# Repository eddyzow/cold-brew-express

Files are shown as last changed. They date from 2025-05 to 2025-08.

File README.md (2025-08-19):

# Cold Brew Express

a DIY electric scooter! Features include variable speed, handlebar throttle, physical brake (not connected in the video), suspension fork for weight distribution, fast top speed, and backlit display for battery.

watch me ride it at https://youtu.be/ShZDwHqLemY?si=LHhTyD6iNOCNyVUB





For links to products in the BOM, go to this google sheet: https://docs.google.com/spreadsheets/d/1F6muKYJhtXkM0ZriuXKycPCZ0PORBCmvhVav8ENI8PE/edit?usp=sharing



## table BOM:

| Item Name | Purpose | Item Source | Quantity | Unit Cost (includes taxes) | Cost | Notes |
|:---|:---|:---|---:|:---|:---|:---|
| 36V 500W 8-Inch Brushless Scooter Hub Motor | Scooter propulsion + back wheel | Amazon | 1 | $109.76 | $109.76 | |
| Brushless Motor Controller 36V 500W 25A | Scooter motion control | Amazon | 1 | $37.18 | $37.18  | |
| 36V 10AH Battery | Scooter power | Amazon | 1 | $99.91 | $99.91  | |
| 8-Inch Pneumatic Scooter Wheel | Scooter front wheel (free-spinning) | Amazon | 1 | $27.61 | $27.61  | |
| 8mm x 150mm Steel Rod | Axle for scooter front wheel | Amazon | 1 | $6.37 | $6.37 | |
| Throttle Accessory | To control motor acceleration | Amazon | 1 | $9.45 | $9.45 | |
| 14-Inch Suspension Fork | For suspension + to connect handlebars to front wheel | Amazon | 1 | $37.50 | $37.50  | |
| 37mm Headset Bearings | To make turning handlebars smoother | Amazon | 1 | $10.63 | $10.63  | |
| 4-Line I2C LCD Display (3) | For visual feedback of speed, battery, other telemetry, etc. | Amazon | 1 | $17.87 | $17.87  | better value than a 1-pack + just in case something goes wrong |
| Flex Seal | Waterproofing housing of the scooter for rain | Home Depot | 1 | $15.92 | $15.92  | |
| Variable PVC Pipe | PVC pipe for handlebars and main steering column | Home Depot | 1 | $21.25 | $21.25  | |
| Variable Plywood | Plywood for base of the scooter + housing of battery and controller | Home Depot | 1 | $21.25 | $21.25  | |
| Wires and Connectors | For wiring electronic components to the microcontroller | Amazon | 1 | $10.63 | $10.63  | primarily JST-SM connectors, jumper wires, bullet-spade connectors. will purchase as needed |
| Screws, Nuts, Bolts | For assembling the components of the scooter together | Home Depot | 1 | $10.63 | $10.63  | |
| TOTAL | | | 14 | $435.96 | $435.96 | |

I already own some necessary parts for this project (arduino, etc) - these are not included in the BOM! I will also gladly pay any surplus costs above the grant amount!

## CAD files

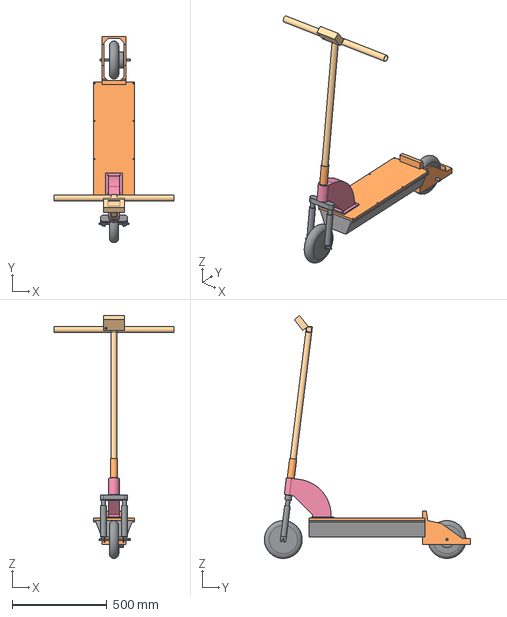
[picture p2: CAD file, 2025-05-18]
CAD Assembly Full.step
632.0 x 1088.6 x 1282.3 mm

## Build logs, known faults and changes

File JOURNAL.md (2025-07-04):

---
title: "The Cold Brew Express"
author: "Eddy Zhao (@eddyzow)"
description: "A DIY electric scooter to take me to Dunkin' Donuts."
created_at: "2025-05-14"
---

# hack club highway project 1: the cold brew express - a diy electric scooter to take me to dunkin'
_can i get a medium raspberry watermelon refresher with sparkling water instead of green tea?_

start date: 5/14/2025

total time spent so far: 43 hrs

# entry 12 (7/3/25)

and with that, the cold brew express is done! while it's not polished, i feel that i can submit becuase it is functionally "sound," i've learned all electronics and engineering that i needed for the project, and i can paint it at any time.

here's a video of me riding it: https://youtu.be/ShZDwHqLemY?si=LHhTyD6iNOCNyVUB

*time spent during session: 1 hour*

# entry 11 (7/2/25)

three home depot trips, multiple PVC pipes, duct tape, wires, and many scares later, the scooter is FUNCTIONAL!!



unfortunately the weight distribution is completely messed up and the scooter has the tendency to do wheelies before actually driving.

nonetheless i'm counting this a success! the battery and controller mounted at the bottom of the scooter. 

i'm so scared the scooter is going to break when i stand on it, so i'm probably not going to make a video of me riding it around. in hindsight I should have printed the head/neck collar with PETG or PLA-CF at the least but it seems like normal PLA is sort of holding up. i replaced multiple parts during the entire process.

the scooter's also super super super super sensitive. i think it could actually go like 20mph at max speed but i'd have to lean forward and put my weight all the way in as front as possible, but the weakest part of the scooter is just behind the front:



while the scooter's still intact, i got some pictures of the scooter.

tomorrow i'll record a demo of the scooter working, but not actualy ride it. if it breaks, then we will consider it a lesson learned. I'll fix it eventually, but undercity is in 9 days and i need to submit this before i leave since i won't be back until highway is nearly over. i'll probably wait until "eventually" to paint the scooter as well

*time spent during session: 6 hours*

# entry 10 (6/29/25)

lots has happened since the last entry... firstly the controller i bought broke (either due to it being bad or me making a mistake), so i had to buy a new one. thankfully, the new one is good, but i need to watch my wiring.

i'm rethinking adding a screen to the scooter. i think it's unnecessary because the throttle i bought has a screen by itself, but maybe just adding a screen for the cool factor could do pretty good. i might be able to use the 5v power supply from the motor controller to power the arduino.

with this sudden realization i discovered that i accidentally plugged in a red wire to the green self-learning plug a few days ago... this might have been what caused the first controller to break. upon reading the datasheet a second time, this red wire (not red in the diagram) actually is connected to the full 36V of the battery!! that means i gave a low-voltage self-learning wire 36 volts and probably fried the controller from there. 

anyways, since the motor works now, i'm going to start putting the final touches together before i flex seal and paint this baby. then, i'm going to ride it around my driveway in a video for proof before submitting it!! unfortunately my parents have forbade me from riding it on public roads (and it's illegal since my permit expired) so i can't go to dunkin with it. after i submit this and my other pull request for my pcb business card (already done) is merged, i'll have 33 highway points!! and there is one more project i wish to do before i leave for undercity -- if i can finish it on time, i'll have 40 points :)

*time spent during session: 7 hours*

# entry 9 (6/19/25)

i designed a lot of new parts! also, the chassis is officially built... just some wiring and testing left to do.



i think that getting the LCD screen incorporated may not be feasible at this moment -- my prime goal is to make sure it drives!

# entry 8 (6/15/25)

re-designed some parts today and planned out how i'm going to build the scooter! here's a picture taken by the camera onboard my bambu p1s:



... and one of the redesigned parts. this will make the weight distribution more compressive. PLA has a quite strong compression resistance, so I bet that 3d-printed parts will be able to do the trick here!



i'm going to put the scooter together in the coming days :D

time spent: about 6 hrs

# entry 7 (6/8/25)
## parts received!

parts have been received for the cold brew express! i'm printing all the 3D printed stuff as I type this -- the last thing to do is to go to home depot and get some plywood, then construct! 

there have been some errors in my planning -- the suspension fork I bought does not have any spring force and also isn't hollow at the top. it's also a little smaller than i expected. i will try to get around that. i wired up the wheel and it seems to work pretty well! the battery works great and the wheel is indeed pretty fast, with high torque. 

*time spent for this session: 2 hrs*

# hack club highway journal entry 6 (5/18/25)
## cad is done!



i believe i've cadded the entirety of the main frame of the scooter! yes, i haven't added things like the throttle but these are the parts that are added to the scooter later as accessories.
wiring will be taped down the side of the handlebar with electrical tape and routed through the hole in the neck between the head tube and the base.

here's what the internals look like:



inside are the battery and controller, which will be mounted in foam. the wires for the motor (rear) will likely be routed through a drilled hole between the rear motor fork and the base, or through the bottom of the base. i've decided that once i start putting the scooter together, i'll decide on things like that.

in the front is a suspension fork that will give the scooter a smoother ride. the display will be a standard 4 line character LCD instead of a full-fledged TFT display since i realized i will need to work with some extremely complicated electronics that i don't have the experience for at the moment. the arduino will also be mounted in the bottom of the scooter. i'm going to need some long ass jumper wires LMFAO

i still don't know how fast the scooter will get, but i'm hoping that it will do 15mph. i'm legally bound to go under 20mph anyways

i'll now be submitting this to the hack club overlords and going off to continue my neighborhood game! i should add that i'm not very experienced with cad and have only in the past imported existing gobilda files and just mated them all together with a minimally designed chassis :sob:

# hack club highway journal entry 5 (5/17/25)
## cad almost done

the CAD is almost done! i ran into a few problems that i've fixed:
- the handlebars are not sized to align with the fork (OD 30mm). i fixed this by custom-creating my own 3D printed "clamp" that will just be superglued to the fork. since i have no interest in folding up the scooter, this will work fine
- 
- i've realized that i needed to CAD the dashboard with the display.

# hack club highway journal entry 4 (5/17/25)
## it's coming together!



as you can see, i've designed many of the parts for the scooter, including the fender and neck / head tube for holding the handlebars. i will purchase a clamp separately to ensure that the handlebars can only turn left-right and cannot move up and down. the last thing i will need to CAD is the suspension fork and then i'll be all set! since i don't know how to produce these parts and i don't necessarily have access to machining tools (my robotics team has a CNC but i don't know how to fabricate the parts more complex than just sheets of metal) i'll be 3D printing them since i'm more familiar with that. 

wires will be fed from my various accessories through the crossbar in a separate tube into the deck. and i will need to secure everything using foam for the interior electronics, screws, and lots of flex seal.

from end to end the scooter is approximately 3.5 ft (1075mm) long and 3 feet (900mm) tall. i came to this value through research on what the typical scooter looks like. i think that i might be able to actually submit this for review after tonight since much of the work is done after the design has already been submitted!

# hack club highway journal entry 3 (5/17/25)
## cad updates + more!



i haven't cadded any special parts yet, like suspension, forks, etc. i think i'll forgo the suspension because apparently all the easy-to-attach suspension forks are for 10-inch wheels, and this scooter is going to have 8-inch wheels. i'll use PVC pipe instead of metal since it's easier to work with.
the part of the deck that the rider stands on is bolted to the battery and controller holder with eight 4mm gobilda screws. i hope this will be enough support.

i've learned that handlebars are angled approx. 83 degrees to the ground, so i have it turned that way.

also, i think i'll actually be 3d printing some parts, such as the fenders for the wheels. i just need to buy some flex seal to waterproof it. i might need to cad forks too, but then my concern is that the forks are not strong enough when 3D printed -- i don't have machine shop knowledge to make custom aluminum forks for my scooter.

i have a full weekend to work, so hopefully i can finish the design soon and get building!

# hack club highway journal entry 2 (5/16/25)
## APPROVED!!
the cold brew express has been approved! i just need to send in a design before i receive my parts. i will get more highway points if i make a project that actually drives!!

i've changed the BOM and feature list to better reflect my hardware knowledge + exact parts i will be getting:
- 36V 500W brushless DC hub motor with wheel and tire included: $104
- 36V 500W motor controller: $35
- 36V 10 amp-hour lithium-ion battery with 30A BMS: $94
- front free-turning wheel and tire: $30
- accessories (i.e. throttle, brake, switches, buttons): about $25
- wires and connectors: about $10
- led 2/4 line display: $10
- rgb light strip/lights: $15
- plywood base: $20
- pvc tubing / wheel forks: $30

i've also begun to create an onshape CAD file for the scooter. i've consulted diagrams of other commercial scooters on the market for inspiration. also many of the parts i'm using have little documentation and no cad files, so i have to make or represent my own objects. here's a picture so far:



no handlebars yet. i am currently hollowing out the bottom of the deck of the scooter so that it can hold the motor controller and battery. 

# hack club highway journal entry 1 (5/15/25)
## introducing the cold brew express: an extremely overengineered custom e-scooter that lets me go get coffee whenever i want!

my goal is to create a modernized e-scooter that is powerful enough to travel 10+ mph and lasts long enough for me to make the 2.5 mile trip to the nearest dunkin’ and back. it will be similar to lime/bird scooters that you find in cities, except it will have some crazy features, including but not limited to the below (i anticipate that i won’t be able to do about half of these due to time/budget constraints):

- automatic start up to cruising speed upon kick off the ground  
- speed controlled via two buttons on either side of the handlebars. press the throttle on the right side to accelerate, press left side to brake  
- press a button to toggle cruise control. during cruise control, an IMU detects for if the scooter is leaning and disengages the autopilot for safety purposes  
- bright LED lights on the front, back, deck, and handlebars of the scooter for riding at night. deck lights will be RGB and controlled by a microcontroller :)  
- telemetry readings all over the scooter, taking data like temperature, speed, battery, miles, etc, fed to an LED/OLED display located on the front driven by an ESP32 microcontroller  
- camera module w/sd card to record trips on the scooter  
- bluetooth support to play music to my airpods directly from the scooter  
- ability to wirelessly charge my phone on the dashboard  
- tactile feedback - handlebars vibrate when braking/accelerating  
- cup holder for dunkin  
- GPS???  

## rough BOM:

- 500-750w brushless hub motor: $70  
- front wheel (rear wheel is attached to the hub motor): $25  
- esc (flipsky vesc 4.2): $50  
- battery pack w/charger (36/48v, 7 ah): $80  
- esp32 CAM microcontroller w/ IR filter ($10)  
- 4 inch display ($15)  
- LED lights (strips + light for head/tail) $20  
- vibration motors ($5)  
- IMU sensor (LSM6DSOX or MPU6050 or BNO055) about $10  
- microsd: $10  
- wireless charging module: $10  
- housing  
- plywood base $20  
- aluminum tubing for support columns and handlebars: $25  
- wires, connectors, switches, nuts, bolts, etc: $20  

**TOTAL: $370\***

\*i fully intend to pay surplus costs out of pocket because i think the cost of this project will exceed $350

as you can see some of these parts are a little pricey… even the core necessities of the scooter cost more than the normal project budget of $150, hence why i believe this falls under the advanced project category.

## design plan:

- research parts and draw inspiration from real electric scooters. identify common escs/batteries/motors for scooters like this one  
- CAD chassis in onshape (plywood deck, aluminum tube supports, handlebars, component layout). ensure parts fit inside enclosure and draw diagrams  
- ensure parts are compatible with each other. voltage compatibility between battery, esc, motor, sensors, and microcontroller, and communication compatibility between sensors and microcontroller  
- design interior layout so that the ESP32 is at the front (hence its camera can be utilized)  

## build plan:

- mechanical assembly. CNC plywood deck, assemble aluminum tubing, drill necessary holes, put enclosure together for the most part, install wheels and hub motor.  
- electrical assembly: lights  
- microcontroller system: wire up microcontroller, connect to various sensors, SPI protocol, configure display, etc  
- features: configure camera to save video clips to sd card, record trip stats, control special lighting, wireless charging, etc  
- weatherproofing: seal enclosures with silicone  
- finally paint the entire thing so that it sports a nice orange and purple color scheme, after my favorite coffee chain :) throw some stickers on and personalize it  
- test ride!! and then take it to dunkin for a nice iced coffee on a hot summer day  

## challenges:

- materials materials materials. metal is expensive and i need to figure out how to optimize the cost of materials for this project without building something dangerous. i’m leaning towards a strong plywood for the base board and metal support bars/steering column for stability. my FTC robotics workshop has a CNC machine that I can use to cut my parts.  
- deciding what motor to use (a BLDC for sure), and figuring how to manage an ESC (i’ve only ever worked with brushed motors)  
- figuring out suspension. i did some research and apparently some scooters don’t have a suspension? but also that using springs to damp some impacts provides for a smoother ride experience  
- i’m not very experienced with electrical work at this level – a vehicle that is powerful enough to carry a human will require an energy current of several amps (or more!) and the battery capacity will need to be ample. good thing my dad is an electrical engineer  
- figuring how how to accel curves so that when starting up and braking i am not thrown off the scooter (this would be very bad)  
- i live in new england ☠️ so i need to make sure the scooter doesn’t explode whether it’s 0 or 100 degrees (F) outside  
- waterproofing the housing so that the scooter is resistant to rain  
- according to massachusetts law i must ride the scooter at a max speed of 15 mph and i need a learner’s permit or a license (whoops im 18 and dont have my license yet 💀)  

i have past experience building robots for FTC and science olympiad – this is taking my love for motorized things to the next level :). it is now 3:30 am and i will sleep because i have school tomorrow.

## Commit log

2025-05-18 Rename Assembly 1.zip to CAD Assembly (All Files).zip
2025-05-18 Rename Assembly 1.step to CAD Assembly (Full)
2025-05-18 Rename CAD Assembly (Full) to CAD Assembly Full.step
    [CAD Assembly Full.step]
2025-05-18 Rename CAD Assembly (All Files).zip to CAD Assembly All Files.zip
2025-05-24 Update and rename Bill of Materials - Cold Brew Express (Ver. 2) - Sheet1.csv to Bill of Materials - Cold Brew Express (Ver. 3) - Sheet1.csv
    [Bill of Materials - Cold Brew Express (Ver. 3) - Sheet1.csv]
